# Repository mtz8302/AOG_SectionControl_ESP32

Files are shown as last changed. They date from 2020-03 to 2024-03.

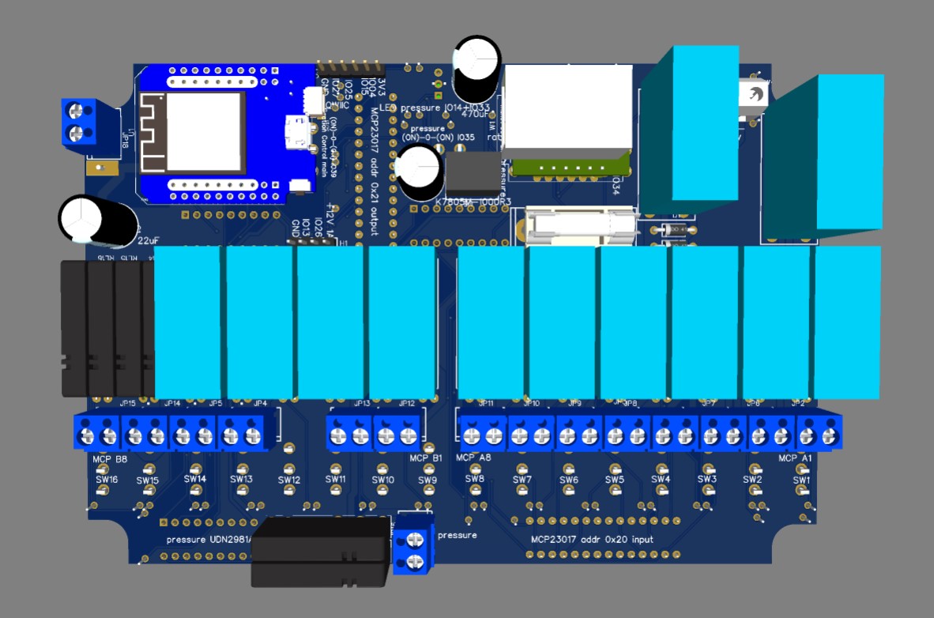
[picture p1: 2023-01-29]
Section control board 16IO/SC16IO board downside.jpg

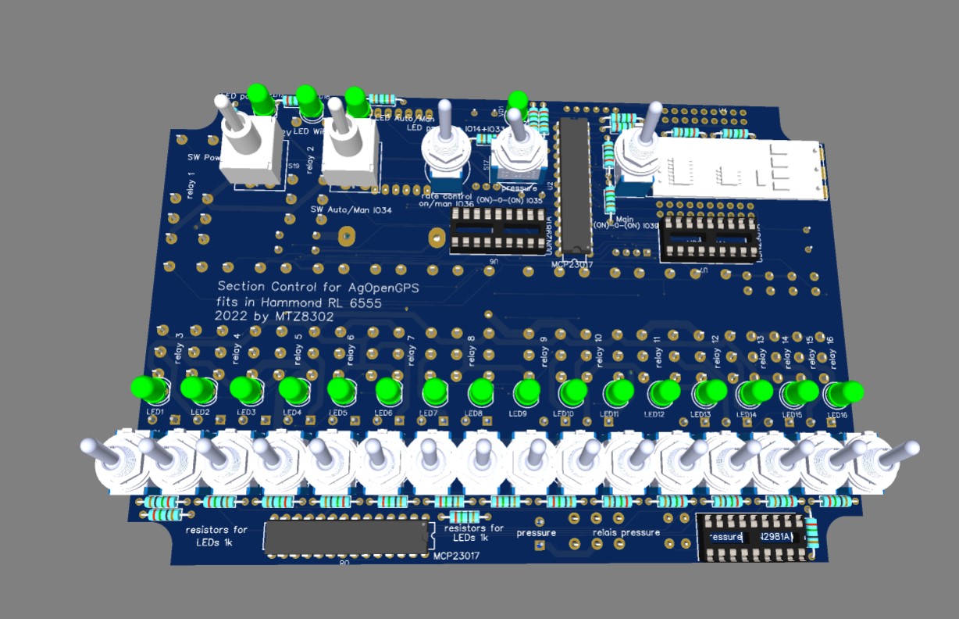
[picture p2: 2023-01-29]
Section control board 16IO/SC16IO board upside.jpg

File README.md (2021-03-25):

# AOG_Section_control

<b>Section Control running on ESP32 for AgOpenGPS PC Software.<br><br>
Multi version code: supports V 4.3.10 (=version code 17) and V5.x.20 (=version code 20)<br>
          
For existing Nano boards, the Upgrade to Nano33iot, to get WiFi is a good solution. Use code for Nano33IoT in other repository.
          
Supports: <br>- Section control, 16 sections
          <br>- hardware input switches (Main ON/OFF, OFF/Auto/ON for each section, +/- pressure (only motor driven, no rate control in V4 so far))
          <br>- documentation only (e.g. for machinery with hydraulic gates)
   <br>and most combinations of it</b>

Settings can be changed via webinterface. The IP adress is x.x.x.71 in your WiFi network. If the log to your networks fails, you wait until an accesspoint is created. Connenct your computer to it and use your browser to get to webinterface at 192.168.1.1

The settings done directly in the code are the default values, that can be reloaded. The pin assigment must be done in the code, most other things can be changed in webinterface.

Make sure, that the SSID and password fits to your tractor's WIFI.

Works with the circuit (by WEder) based on Arduino nano, see PDF.

<b>!!!The ESP32 and the Nano33 iot use 3.3V for any in-/outputs !!!</b>

A suggestion for ESP32 pinout is in the PDF. Don't use pins GPIO 0, 6-12. The pins 33-39 are input only, and don't have pullup resistors.

<b>Further remarks on the ESP32 pinout:</b><br>
The circuit could be mostly the same as in WEder's schematic.

All switches use internal pullup, so switch to GND.

GPIO 39 has no internal pullup, so external resistor 10k to 3.3V and switch to GND.

Pressure(Flowrate) and Main Switch are (ON)-OFF-(ON) switches or push buttons: 3.3V - 1.15V - GND to get 1.15V use 10k to 3.3 and 10k to GND. So only 1 input for 2 functions is needed.

For the outputs use a driver like UDN2981(relais have common GND and UDN does +) or ULN2803 (relais have common + and ULN does GND) 

Remark on non booting ESP32: they don't like raising input voltage when powering your step down 3,3V power source. To keep them in reset, put a 10uF electrolytic capacitor to reset - GND and another one EN - GND. So the enable and the reset pin will be LOW until power is stable. With this they will boot.

NO rate control in this code at the moment (not supported by AOG)

Suggestion for documentation only: https://agopengps.discourse.group/t/section-control-documentation-for-ferilizer-spreader/1360

Suggestion for upgrading Mueller spray controller: https://agopengps.discourse.group/t/muller-spray-controll-with-motor-valves/1303

Video how to use switches: https://youtu.be/kI321iBwe4U

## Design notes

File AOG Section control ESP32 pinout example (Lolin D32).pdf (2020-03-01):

## no analog Input while WiFi use (A2 occupied)

# AgOpenGPS

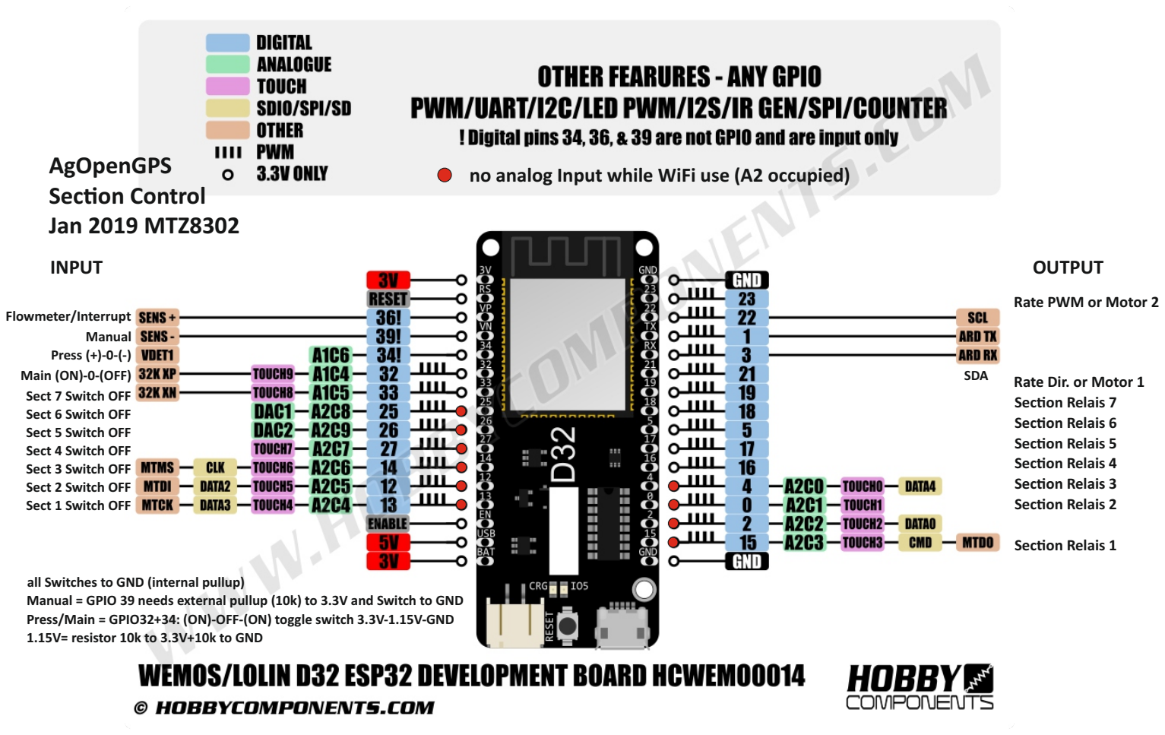
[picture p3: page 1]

SDA

## INPUT

Flowmeter/Interrupt
Manual
Press (+)-0-(-)
Main (ON)-0-(OFF)
Sect 7 Switch OFF
Sect 6 Switch OFF
Sect 5 Switch OFF
Sect 4 Switch OFF
Sect 3 Switch OFF
Sect 2 Switch OFF
Sect 1 Switch OFF

Rate Dir. or Motor 1

Rate PWM or Motor 2

Secon Relais 2

Secon Relais 1

Secon Relais 3

Secon Relais 4

Secon Relais 5

Secon Relais 6

Secon Relais 7

## OUTPUT

# Secon Control Jan 2019 MTZ8302

all Switches to GND (internal pullup)
Manual = GPIO 39 needs external pullup (10k) to 3.3V and Switch to GND Press/Main = GPIO32+34: (ON)-OFF-(ON) toggle switch 3.3V-1.15V-GND 1.15V= resistor 10k to 3.3V+10k to GND

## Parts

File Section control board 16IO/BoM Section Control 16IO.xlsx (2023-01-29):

BoM Section Control 16IO
MTZ8302
 |  |  |  |  |  |  |  |  | 2022-07-24
ID | Name | Designator | Footprint |  | Quantity | Supplier | Supplier Part | Price per unit | price | sub-total
PCB by JLCPCB |  |  |  |  | 1 | MTZ8302/JLCPCB |  | 45.00 € | 45.00 € | 45.00 €
parts for PCB
PCB - Power supply
 | 22uF | C1 | CAP-D10.0-F5.0 |  | 1 | Conrad | 468240 - 62 | 0.26 € | 0.26 €
 | 470uF | C2 | CAP-D10.0-F5.0 |  | 1 | Conrad | 468134 - 62 | 1.59 € | 1.59 €
 | 22uF | C3 | CAP-D10.0-F5.0 |  | 1 | Conrad | 468240 - 62 | 0.26 € | 0.26 €
 | 1A | F1 | FUSE-HOLDER-WITH-COVER-FOR-5X20MM-FUSE_FOOTPRINT |  | 1 | Conrad | 530127 - 62 | 0.39 € | 0.39 €
 | 1N4007GU | D2,D1 | DO-41_BD2.4-L4.7-P8.70-D0.9-RD |  | 2 | Conrad | 162272 | 0.08 € | 0.16 €
 | K7805M-1000R3 | U5 | PWRM-TH_K7805M-1000R3 |  | 1 | Digikey | 2725-7805m-1000r3-nd | 3.12 € | 3.12 €
 | 2 pol 5mm screw terminal | JP1,JP2,JP3,JP4,JP5,JP6,JP7,JP8,JP9,JP10,JP11,JP12,JP13,JP14,JP15,JP16,JP18 | SCREWTERMINAL-5MM-2 | Power + rate + 1 per section | 1 | Conrad | 1430098 | 0.40 € | 0.40 €
 | 1A fuse 5x20mm |  |  |  | 1 | Conrad | 1576534 | 0.16 € | 0.16 €
 | APEM 5546A 2x I/I | S19,S20 | SWITCH_DPDT_LEVER | Power + SC auto/man | 2 | Conrad | 700378 | 5.99 € | 11.98 €
 |  |  |  |  |  |  |  |  |  | 18.32 €
ESP32, MCP, driver, Ethernet
 | WEMOS-D1 MINI ESP32 | U1 | WEMOS-ESP32 D1 MINI |  | 1 | Amazon | WEMOS_S2_MINI | 9.98 € | 9.98 €
 | Wiznet W5500 Lite Module | W1 | W5500 LITE MODULE MINI |  | 1 | Amazon |  | 12.87 € | 12.87 €
 | UDN2981A-T | U10,U6,U7 | DIP-18_L22.9-W10.2-P2.54-LS7.6-BL |  | 3 | reichelt | UDN291 | 1.04 € | 3.12 €
 | Socket DIP-18 |  |  |  | 3 | Conrad | 189537 | 0.24 € | 0.72 €
 | MCP23017 Addr 0x20 | U8 | DIL28-3-ROUND |  | 2 | Conrad | 651440 | 1.58 € | 3.16 €
 | Socket 28pol 7,62mm | U2 |  |  | 2 | Conrad | 189515 | 0.36 € | 0.72 €
 | RS485_to_TTL_2 | U4 | RS485_TO_TTL |  | 0 | Arceli |  |  | 0.00 €
 | LED5MM | LED17,LED16,LED12,LED11,LED10,LED9,LED8,LED7,LED6,LED5,LED4,LED3,LED2,LED1,LED13,LED15,LED14 | LED5MM | 1 per section + 1 power + 1 wifi | 2 | Conrad (gn) | 1526857 | 0.28 € | 0.56 €
 |  |  |  |  |  |  |  |  |  | 31.13 €
connectors
 | 2 pol 5mm screw terminal | JP1,JP2,JP3,JP4,JP5,JP6,JP7,JP8,JP9,JP10,JP11,JP12,JP13,JP14,JP15,JP16,JP18 | SCREWTERMINAL-5MM-2 | Power + rate + 1 per section | 17 | Conrad | 1430098 | 0.40 € | 6.80 €
 | 6-PPIN-HEADER | U3 | 6-PIN-CONNECTOR-HEADER |  | 1 |  |  | 0.20 € | 0.20 €
 | SM04B-SRSS-TB(LF)(SN) | J1 | CONN-SMD_SM04B-SRSS-TB | Qwiic | 0 |  |  |  | 0.00 €
 | Header-Male-2.54_1x4 | H1 | HDR-TH_4P-P2.54-V-M |  | 1 |  |  | 0.10 € | 0.10 €
 |  |  |  |  |  |  |  |  |  | 7.10 €
parts for sections |  | 6 | sections
 | Finder-34.51.7.012.0010 | RL16,RL15,RL14,RL13,RL17,RL18 | FP_FINDER-SINGLEROW | 2x rate + section 13,14,15,16 | 0 | Conrad | 502867 | 6.49 € | 0.00 €
 | FINDER-41.52.9.012.0010 | RL12,RL11,RL10,RL9,RL8,RL7,RL6,RL5,RL4,RL3,RL2,RL1 | RELAY-FINDER-41.52 COPY | sections 1 - 12 | 6 | Conrad | 403105 | 5.54 € | 33.24 €
 | 1k | R29,R19,R18,R17,R16,R12,R11,R10,R9,R8,R7,R6,R5,R4,R3,R2,R1,R15,R14,R13,R28,R27,R26,R25,R24 | RES-TH_BD2.4-L6.3-P10.30-D0.6 |  | 10 | Conrad | 1557045 | 0.10 € | 1.00 €
 | 1k8 | R30 | RES-TH_BD2.4-L6.3-P10.30-D0.6 |  | 0 | Conrad | 1557364 | 0.10 € | 0.00 €
 | APEM 5537A 1x (I)/0/(I) | S17,S18 | SWITCH_SPDT_LEVER | SC Main on/off + rate | 2 | Conrad | 700351 | 4.29 € | 8.58 €
 | APEM 5536A 1x I/I | S21,S16,S15,S14,S13,S12,S11,S10,S9,S8,S7,S6,S5,S4,S3,S2,S1 | SWITCH_SPDT_LEVER | 1 per section + 1 rate auto/man | 6 | Conrad | 700337 | 4.29 € | 25.74 €
 | 2 pol 5mm screw terminal | JP1,JP2,JP3,JP4,JP5,JP6,JP7,JP8,JP9,JP10,JP11,JP12,JP13,JP14,JP15,JP16,JP18 | SCREWTERMINAL-5MM-2 | Power + rate + 1 per section | 6 | Conrad | 1430098 | 0.40 € | 2.40 €
 | BiColorLED-AKA | VD2,VD0 | LED_BICOL_AKA_4 |  | 1 | Conrad (ge/gn) | 1577518 | 0.59 € | 0.59 €
 | LED5MM | LED17,LED16,LED12,LED11,LED10,LED9,LED8,LED7,LED6,LED5,LED4,LED3,LED2,LED1,LED13,LED15,LED14 | LED5MM | 1 per section + 1 power + 1 wifi | 6 | Conrad (gn) | 1526857 | 0.28 € | 1.68 €
 | 10k | R23,R22,R21,R20 | RES-TH_BD2.4-L6.3-P10.30-D0.6 |  | 4 | Conrad | 400378 | 0.11 € | 0.44 €
 | LED5MM | LED17,LED16,LED12,LED11,LED10,LED9,LED8,LED7,LED6,LED5,LED4,LED3,LED2,LED1,LED13,LED15,LED15 | LED5MM |  | 0 | Conrad (ge) | 1603104 | 0.15 € | 0.00 €
 |  |  |  |  |  |  |  |  |  | 73.67 €
parts for rate
 | Finder-34.51.7.012.0010 | RL16,RL15,RL14,RL13,RL17,RL18 | FP_FINDER-SINGLEROW | 2x rate + section 13,14,15,16 | 2 | Conrad | 502867 | 6.49 € | 12.98 €
 | APEM 5537A 1x (I)/0/(I) | S17,S18 | SWITCH_SPDT_LEVER | rate +/- | 1 | Conrad | 700351 | 4.29 € | 4.29 €
 | APEM 5536A 1x I/I | S21,S16,S15,S14,S13,S12,S11,S10,S9,S8,S7,S6,S5,S4,S3,S2,S1 | SWITCH_SPDT_LEVER | rate auto/man | 1 | Conrad | 700337 | 4.29 € | 4.29 €
 | 2 pol 5mm screw terminal | JP1,JP2,JP3,JP4,JP5,JP6,JP7,JP8,JP9,JP10,JP11,JP12,JP13,JP14,JP15,JP16,JP18 | SCREWTERMINAL-5MM-2 | Power + rate + 1 per section | 1 | Conrad | 1430098 | 0.40 € | 0.40 €
 | BiColorLED-AKA | VD2,VD1 | LED_BICOL_AKA_5 |  | 1 | Conrad (rt/gn) | 1577346 | 0.59 € | 0.59 €
 |  |  |  |  |  |  |  |  |  | 22.55 €
housing
 | hammond 6555 |  |  |  | 1 | conrad | 531864 | 10.55 € | 10.55 €
 |  |  |  |  |  |  |  |  |  | 10.55 €
 |  |  |  |  |  |  |  |  |  |  | 208.32 € | PCB with components and box
cabeling
 | 2 x 2.5 Lapp Ölflex classic 110 |  |  | power supply | 2 | conrad | 601836 | 3.29 € | 6.58 €
 | 25G 0.75 Ölflex classic 110 |  | maybe less wires | box to sprayer | 6 | conrad | 600248 | 9.49 € | 56.94 €
 | M16 Lapp Kabelverschraubung |  |  |  | 1 | Conrad | 127713 | 1.29 € | 1.29 €
 | M25 Lapp Kabelverschraubung |  |  |  | 2 | Conrad | 527739 | 2.29 € | 4.58 €
 |  |  |  |  |  |  |  |  |  | 69.39 €
connector for Arag
 | Hirschmann GM 209 NJ |  |  |  | 8 | Conrad | 734958 | 2.79 € | 22.32 €
 |  |  |  |  |  |  |  |  |  | 22.32 €
power connector
 | Hella 8JA 002 263-011 |  |  |  | 1 |  |  | 9.63 € | 9.63 €
 |  |  |  |  |  |  |  |  |  | 9.63 €
 |  |  |  |  |  |  |  |  |  | 309.66 €

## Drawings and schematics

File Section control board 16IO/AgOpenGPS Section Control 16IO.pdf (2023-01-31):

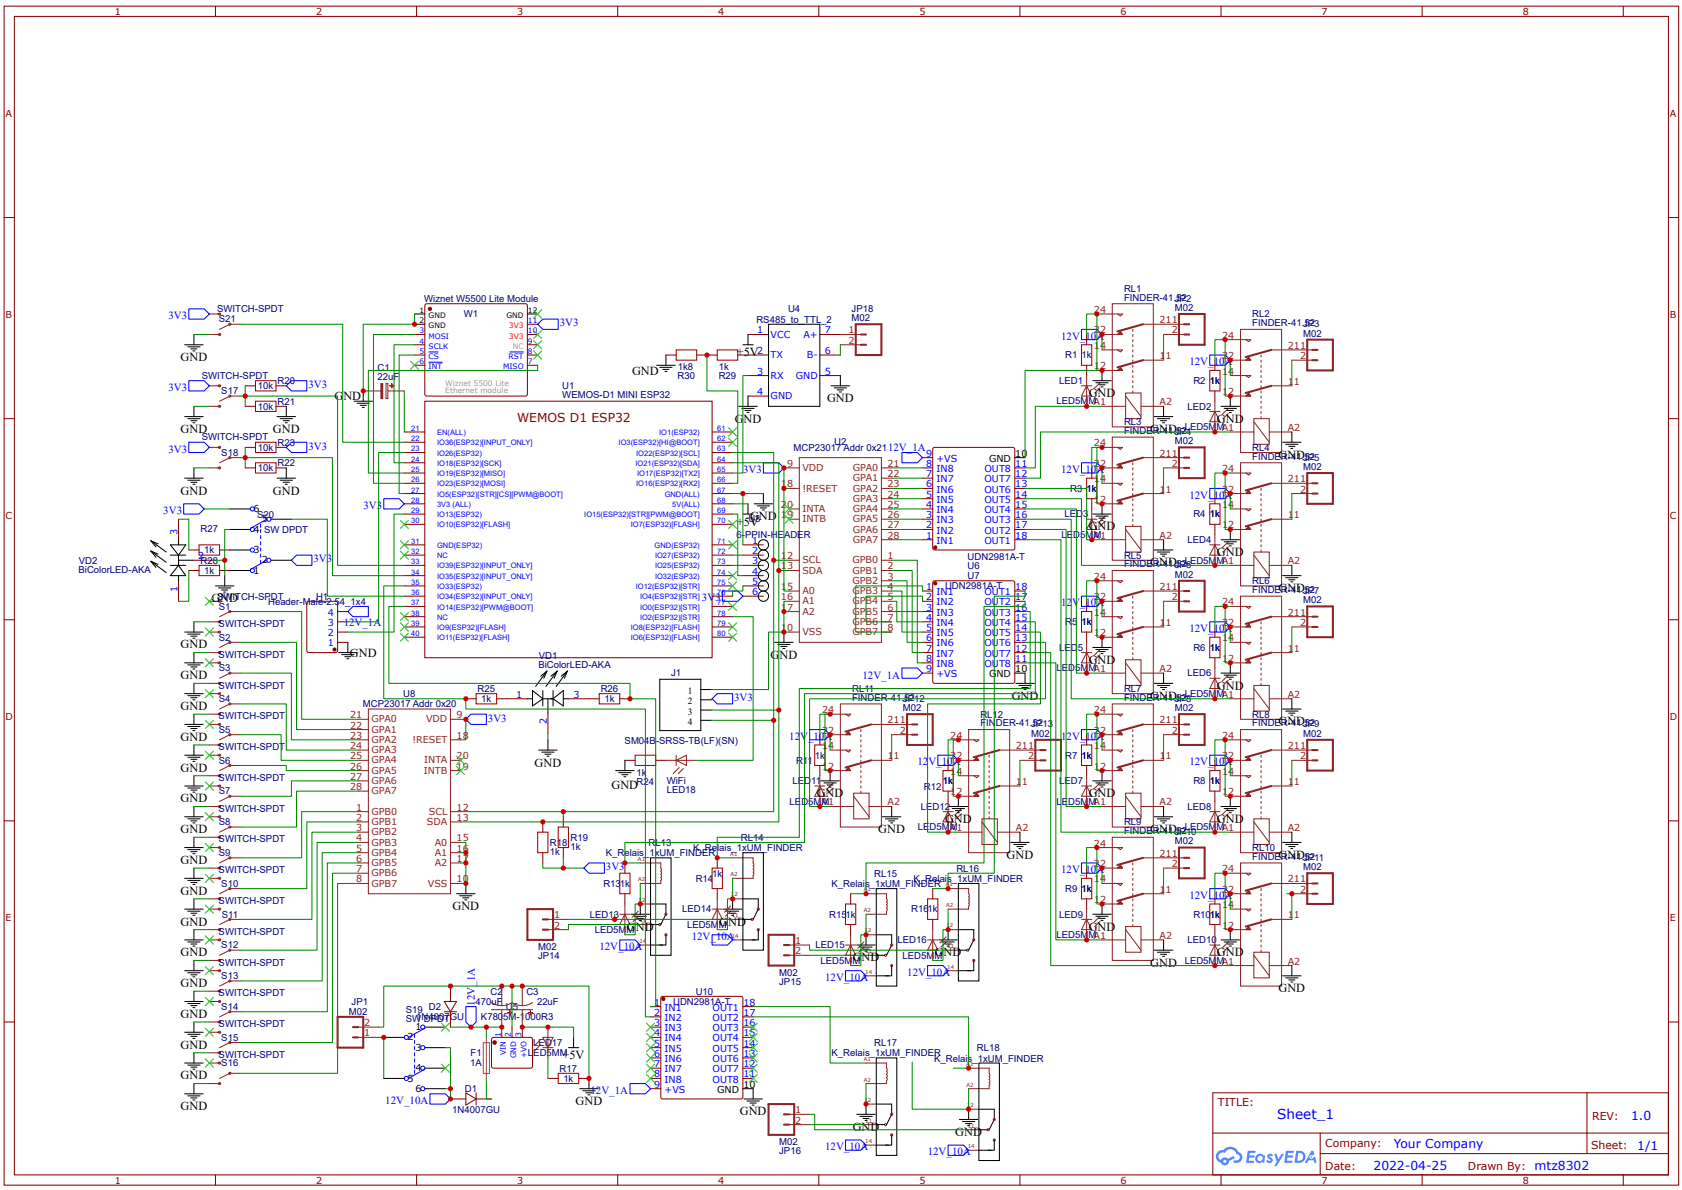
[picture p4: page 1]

SM04B-SRSS-TB(LF)(SN)

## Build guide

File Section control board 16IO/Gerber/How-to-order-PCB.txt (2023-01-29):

How to Order PCB

Please refer to:
https://docs.easyeda.com/en/PCB/Order-PCB

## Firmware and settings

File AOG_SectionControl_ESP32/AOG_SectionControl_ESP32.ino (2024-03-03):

// Section Control code for AgOpenGPS V5 or later for ESP32

// by MTZ8302 see GitHub https://github.com/mtz8302 and Youtube Ma Ha MTZ8302 https://www.youtube.com/channel/UCv44DlUXQJKbQjzaOUssVgw

// can be used as output only = relais for sections
// or for documentation = input only = input to ESP32 -> enables mapping for active (=switch to GND) section in AOG
// or any combination = section control with input switch
// main and pressure switches are (ON)-0-(ON) toggle switches (GND)- 1.75V - (3,3V). So use 2 resistors GND- 1K - (COM on toggle switch) - 1K - 3.3V
// section switches and auto/manual switch are ON-OFF switches

// connects to existing WiFi network or creates access point. Settings below or in WebInterface at 192.168.1.71 in access point mode Webinterface at 192.168.1.1

// while startup ESP32 sends debug infos to USB at 38400 baud

byte vers_nr = 58;
char VersionTXT[150] = " - 28. Feb 2024 by MTZ8302<br>PCA9555, AgIO Heartbeat, AsyncUDP for WiFi, multiple WiFi networks, Ethernet support";


struct set {
	//User config: ***********************************************************************************

	uint8_t DataTransVia = 10;		//transfer data via 0 = USB / 7 = WiFi / 10 = Ethernet UDP
	uint8_t aogVersion = 20;		// not used at the moment
	uint8_t AgIOHeartbeat_answer = 1;//0: don't send (default)
	uint8_t LEDWiFi_PIN = 2;		// WiFi Status LED 255 = off
	uint8_t LEDWiFi_ON_Level = 1;   // 1 = HIGH = LED on high, 0 = LOW = LED on low

	//WiFi---------------------------------------------------------------------------------------------
	//tractors WiFi or mobile hotspots. Connections are checked in this order
	char ssid1[24] = "Matthias A53";	// WiFi network Client name
	char password1[24] = "aveasillrac";                // WiFi network password//Accesspoint name and password
	char ssid2[24] = "Deutz_6006";			// WiFi network Client name
	char password2[24] = "";                // WiFi network password//Accesspoint name and password
	char ssid3[24] = "Fendt_209V_Tablet";					// WiFi network Client name
	char password3[24] = "Fendt_209V";                // WiFi network password//Accesspoint name and password
	char ssid4[24] = "Fendt_209V";					// WiFi network Client name
	char password4[24] = "";                // WiFi network password//Accesspoint name and password
	char ssid5[24] = "WLANHammer";					// WiFi network Client name
	char password5[24] = "aveasillrac";                // WiFi network password//Accesspoint name and password

	char ssid_ap[24] = "SectionControlNet"; // name of Access point, if no WiFi found, no password!!
	uint8_t timeoutRouter = 20;//s         // time (s) to search for existing WiFi, then starting Accesspoint 
	byte timeoutWebIO = 10;//min  		    // time (min) afterwards webinterface is switched off	
	uint8_t timeoutRouterEth = 255;//s		// time (s) to search for Ethernet cable, then changing datatransfer to WiFi

	//WiFi
	byte WiFi_myip[4] = { 192, 168, 137, 71 };    // Section Control 
	byte WiFi_gwip[4] = { 192, 168, 1, 1 };     // Gateway IP only used if Accesspoint created
	byte WiFi_ipDest_ending = 255;				//ending of IP address to send UDP data to
	byte mask[4] = { 255, 255, 255, 0 };
	byte myDNS[4] = { 8, 8, 8, 8 };				//optional

	//Ethernet
	byte Eth_myip[4] = { 192, 168, 5, 72 };     // Section Control 
	byte Eth_ipDest_ending = 255;				// ending of IP address to send UDP data to
	byte Eth_mac[6] = { 0x90,0xA2,0xDA,0x10,0xB3,0x1B };
	bool Eth_static_IP = false;					// false = use DHPC and set last number to 80 (x.x.x.80) / true = use IP as set above

	uint16_t PortSCToAOG = 5555;			// this is port of this module: Autosteer = 5577 IMU = 5566 Section Control = 5555 GPS = 5544
	uint16_t PortFromAOG = 8888;            // port to listen for AOG
	uint16_t PortDestination = 9999;        // Port of AOG that listens
	uint16_t BaudRate = 38400;              // Baudrate = speed of serial port or USB or Bluetooth. AOG uses 38400 for UART

//the following lines should be configed by the user to fit the programm to the sprayer/ESP32
//GPIOs of the ESP32 (current setting is for the layout shown as example WIKI)

	byte Eth_CS_PIN = 5;// 13;					// CS PIN with SPI Ethernet hardware  SPI config: MOSI 23 / MISO 19 / CLK18 / CS5
	byte Eth_INT_PIN = 255;                 //interupt pin not used at the moment, but needed if async ethernet lib will be used

// if only 1 flowrate is used, use left
//Example1: motor valve is controled only by Switch not by AOG, no Flowmeter, : RateControl..Equiped = false; RateSW..Equiped = true; RateControlPWM = false;
//Example2: PWM valve, with flowmeter all controled by AOG:   RateControl..Equiped = true; RateSW..Equiped = true; RateControlPWM = true;	
	uint8_t RateControlLeftInst = 0;		// 1 if Rate control is there, else: 0
	uint8_t RateSWLeftInst = 1;				// 1 if Rate control Pressure switch is there, else: 0
	uint8_t RateSWLeft_PIN = 39;// 34;			// Rate +/- switch (ON)-0-(ON) toggle switch (GND)- 1.75V - (3,3V)
	uint8_t RateControlPWM = 0;				// 1 if PWM valve, 0 if Motor drive for pressure change		

	uint8_t	FlowDirLeft_PIN = 32;// 23;			// Rate-Control Valve/Motor Direktion
	uint8_t	FlowPWMLeft_PIN = 33;// 22;			// Rate-Control Valve PWM/Motor ON/OFF
	uint8_t	FlowEncALeft_PIN = 255;			// Flowmeter left/1

	uint8_t RateControlRightInst = 0;	    // 1 if Rate control is there, else: 0
	uint8_t RateSWRightInst = 0;			// 1 if Rate control Pressure switch is there, else: 0	
	uint8_t	RateSWRight_PIN = 255;			// Rate +/- switch
	uint8_t	FlowDirRight_PIN = 255;			// 255  = unused Rate-Control Valve Direktion
	uint8_t	FlowPWMRight_PIN = 255;			// 255  = unused Rate-Control Valve PWM
	uint8_t	FlowEncARight_PIN = 255;		// Flowmeter right/2 

	uint8_t SectNum = 16;					// number of sections
	uint8_t SectRelaysInst = 1;				// relays for SC output are equiped (0=no output, only documentation)
	uint8_t SectRelaysON = 1;				// relays spray on 1 or 0 (high or low)
	//Relay_PIN = GPIOs of ESP32 OUT to sections of sprayer, 255 = unused, 100 = pin IO 1 on PCA9555 116 = pin IO 16 on PCA9555
	uint8_t Relay_PIN[16] = { 100,101,102,103,104,105,106,107,108,109,110,111,112,113,114,115 };// { 15, 2, 0, 4, 16, 17, 18, 19, 21, 255, 255, 255, 255, 255, 255, 255 };
	uint8_t Relais_MainValve_PIN = 0;// 255;		// PIN for Main fluid valve 255 = unused
	
	uint8_t SectSWInst = 1;					// 1 if section input switches are equiped, else: 0	
	uint8_t SectSWAutoOrOn = 1;				// Section switches spray/auto on 1 = high = used with pullup, 0 = low = pulldown 
	uint8_t SectSW255Stat = 2;				// not present switches (255) send 0 = auto, 1 = on, 2 = off, (comming soon: 3 = undefined) 
	//section switches to GPIOs of ESP32, 255 = unused, 100 = pin IO 1 on PCA9555 116 = pin IO 16 on PCA9555
	uint8_t SectSW_PIN[16] = { 100,101,102,103,255,105,106,107,108,255,110,111,112,113,114,115 };// { 255, 12, 14, 27, 26, 25, 33, 255, 36, 255, 255, 255, 255, 255, 255, 255 };
	uint8_t	SectMainSWType = 1;				// 0 = not equiped 1 = (ON)-OFF-(ON) toggle switch or push buttons 2 = connected to hitch level sensor 3 = inverted hitch level sensor
	uint16_t	HitchLevelVal = 2000;		// Value for hitch level: switch AOG section control to Auto if lower than... ESP:2000 nano 500
	uint8_t	SectMainSW_PIN = 35;// 32;			// ESP32 to AOG Main auto toggle switch open=+1,9V=nothing/AOG button GND=OFF +3,3=AOG Auto on	OR connected to hitch level sensor	
	uint8_t	SectAutoManSW_PIN = 34;// 39;			// Main Auto/Manual switch 39:!!no internal pullup!!

	uint8_t DualFluidSW_PIN = 255;			//not supported at the moment
	uint8_t OnOffDelayAutoManSW_PIN = 255;	//not supported at the moment
	uint8_t OnDelayDist_dm = 30;			//not supported at the moment
	uint8_t OffDelayDist_dm = 35;			//not supported at the moment

	uint8_t DocOnly = 0;					// 0: use as section control, 1: Documentation only = AOG writes the state of the input switches

	uint8_t I2CAddrPCAInput = 0x20;
	uint8_t I2CAddrPCAOutput = 0x21;

	uint8_t resByte0 = 0;
	uint8_t resByte1 = 0;
	uint8_t resByte2 = 0;
	uint8_t resByte3 = 0;

	uint16_t resInt0 = 0;
	uint16_t resInt1 = 0;

	bool debugmode = false;
	bool debugmodeRelay = false;
	bool debugmodeSwitches = false;
	bool debugmodeDataFromAOG = false;
	bool debugmodeDataToAOG = false;

	// END of user config ****************************************************************************
}; set Set;


bool EEPROM_clear = false;



byte SCToAOG[14] = { 0,0,0,0,0,0,0,0,0,0,0,0,0,0 }, SCToAOGOld[14] = { 0,0,0,0,0,0,0,0,0,0,0,0,0,0 };
uint8_t helloFromSC[] = { 128, 129, 123, 123, 5, 0, 0, 0, 0, 0, 71 }; //hello from SC sent back to AgIO

const byte FromAOGSentenceHeader[3] = { 0x80,0x81,0x7F };
#define FromSCHeader 0x7B
#define SCDataToAOGHeader  0xEA
#define SteerDataFromAOGHeader  0xFE  //take section info from steer packet
#define SCSettingsFromRCHeader  0xFC
#define AgIO_heartbeat 0xC8
#define AgIO_ScanRequest 0xCA//AgIO asking for IP -> Ethernet/WiFi GPS sends IP 
#define SCDataSentenceToAOGLength  14

//write incoming Data to sentence array if it fits in
#define SentenceFromAOGMaxLength 14
byte SentenceFromAOG[SentenceFromAOGMaxLength], SentenceFromAOGLength;

//global, as serial/USB may not come at once, so values must stay for next loop
byte incomSentenceDigit = 0,DataToAOGLength;
bool isSteerDataFound = false, isRCSettingFound = false, isAgIOHeartbeatFound = false, isAgIOScanRequestFound = false;

#define incommingDataArraySize 10
byte incommingBytes[incommingDataArraySize][500], incommingBytesArrayNr = 0, incommingBytesArrayNrToParse = 0;
unsigned int incommingDataLength[incommingDataArraySize] = { 0,0,0,0,0 };

//WIFI+Ethernet
IPAddress WiFi_ipDestination, Eth_ipDestination; //set in network.ino
byte Eth_connect_step, WiFi_connect_step = 10, WiFi_netw_nr = 0, WiFi_STA_connect_call_nr = 0, my_WiFi_Mode = 0; // WIFI_STA = 1 = Workstation  WIFI_AP = 2  = Accesspoint
//int pingResult, WiFiWatchDog = 0;
bool WiFiUDPRunning = false, EthUDPRunning = false, task_WiFiConnectRunning = false;
unsigned long WebIOTimeOut = 0, WiFi_network_search_timeout = 0, Eth_network_search_timeout = 0;//PingToNetworkLastTime = 0,
//webpage
long argVal = 0;
bool WebIORunning = false;

// WiFi LED blink times: searching WIFI: blinking 4x faster; connected: blinking as times set; data available: light on; no data for 2 seconds: blinking
unsigned int LED_WIFI_time = 0;
unsigned int LED_WIFI_pulse = 2000;   //light on in ms 
unsigned int LED_WIFI_pause = 1500;   //light off in ms
boolean LED_WIFI_ON = false;
unsigned long timeout, timeout2;



//ToDo: - Rate / flowmeter doesn't work, interrupt mode ect not defined
//      - line 260 PWM + Interrupt mode ect...
//		  - Right side Rate caluclation / output / Motordrive
//      - Manual mode for Rate Control
//		  - what to do if no WIFI??


//libraries -------------------------------
#include "EEPROM.h"
#include "Update.h"
#include <WiFi.h>
#include <AsyncUDP.h>
#include <WebServer.h>
#include <Wire.h>
#include <Ethernet.h>
#include "zAOG_ESP32Ping.h"
#include "zAOG_ping.h"

WebServer WiFi_Server(80);
AsyncUDP WiFiUDPFromAOG;
AsyncUDP WiFiUDPToAOG;
EthernetUDP EthUDPToAOG;
EthernetUDP EthUDPFromAOG;
TaskHandle_t taskHandle_Eth_connect;
TaskHandle_t taskHandle_WiFi_connect;
TaskHandle_t taskHandle_DataFromAOGUSB; bool USBDataTaskRunning = false;
TaskHandle_t taskHandle_DataFromAOGEth; bool EthDataTaskRunning = false;
TaskHandle_t taskHandle_WebIO;
TaskHandle_t taskHandle_LEDBlink;


//values to decide position of section switch
#define SWOFF 650 // analog in is lower than .. for off
#define SWON 3000 // analog in is lower than .. for auto/on


//analog value of the toggle switches (default: middle=unpressed)
int MainSWVal = (SWOFF + SWON) / 2;
int MainSWValOld = (SWOFF + SWON) / 2;
int RateSWLeftVal = (SWOFF + SWON) / 2;
int RateSWRightVal = (SWOFF + SWON) / 2;

//state of the switches HIGH = ON/Auto LOW = OFF	
boolean SectSWVal[16] = { HIGH,HIGH,HIGH,HIGH,HIGH,HIGH,HIGH,HIGH,HIGH,HIGH,HIGH,HIGH,HIGH,HIGH,HIGH,HIGH };
boolean AutoSWVal = HIGH;
byte debugmodeSwitchesBak = 3;  //0 = false 1 = true 3 = not used

//loop time variables in microseconds
const unsigned long LOOP_TIME = 500; //in msec; 1000 = 1 Hz
const unsigned long SectSWDelayTime = 200;//time the arduino waits after manual Switch is used before acception command from AOG in msec
unsigned long lastTime = LOOP_TIME;
unsigned long now = LOOP_TIME;
unsigned long DataFromAOGTime = 0;
unsigned long SectAutoSWTime = LOOP_TIME;
unsigned long SectAutoSWlastTime = LOOP_TIME;
unsigned long SectMainSWlastTime = LOOP_TIME;
unsigned long RateSWlastTimeLeft = LOOP_TIME;
unsigned long RateSWDelayTime = 250; //time to pass before a new toggle of switch is accepted = if hold down, time between steps
unsigned long RateSWlastTimeRight = LOOP_TIME;
unsigned long SectSWcurrentTime = LOOP_TIME;


/* no rate control in AOG
//Kalman variables Left
float rateKLeft = 0;
float PcLeft = 0.0;
float GLeft = 0.0;
float PLeft = 1.0;
float XpLeft = 0.0;
float ZpLeft = 0.0;
float XeRateLeft = 0; //the filtered flowrate
const float varRateLeft = 100; // variance, smaller, more filtering
const float varProcessLeft = 10;

//Kalman variables Right
float rateKRight = 0;
float PcRight = 0.0;
float GRight = 0.0;
float PRight = 1.0;
float XpRight = 0.0;
float ZpRight = 0.0;
float XeRateRight = 0; //the filtered flowrate
const float varRateRight = 100; // variance, smaller, more filtering
const float varProcessRight = 10;
*/

//program flow
//bool NewDataFromAOG = false, NewSettingFromAOG = false;

//bit 0 on byte[0] is section 1
byte SectGrFromAOG[] = { 0, 0 }; //Sections ON / OFF Bitwise !!! 
byte RelayOUT[] = { 0,0 }; //Sections ON / OFF Bitwise !!! 
byte RelayOUTOld[] = { 0,0 };
byte SectSWOffToAOG[] = { 0,0 };
byte SectMainToAOG = 0;
byte uTurnRelay = 0;
//  byte flowRateSW1 = 0;
boolean PCAinUse = false;
boolean SectMainSWpressed = false;
boolean SectSWpressed = false;
boolean SectSWpressedLoop = false;
boolean SectAuto = true;
boolean SectAutoOld = true;
boolean SectAutoSWpressed = false;
//boolean RateAuto = false;
boolean RateManUpLeft = false;
boolean RateManUpRight = false;
boolean RateManDownLeft = false;
boolean RateManDownRight = false;

boolean SectMainOn = false;

boolean newDataToAOG = false;// newDataFromAOG = false;

float gpsSpeed = 0; //speed from AgOpenGPS
float rateSetPointLeft = 0.0;
float countsThisLoopLeft = 0;
float rateErrorLeft = 0; //for PID
int rateAppliedLPMLeft = 0;
float rateSetPointRight = 0.0;
float countsThisLoopRight = 0;
float rateErrorRight = 0; //for PID
int rateAppliedLPMRight = 0;

unsigned long accumulatedCountsLeft = 0;
float flowmeterCalFactorLeft = 50;
unsigned long accumulatedCountsRight = 0;
float flowmeterCalFactorRight = 50;
unsigned long accumulatedCountsDual = 0;

float pulseAverageLeft = 0;
float pulseAverageRight = 0;

//the ISR counter
volatile unsigned long pulseCountLeft = 0, pulseDurationLeft;
volatile unsigned long pulseCountRight = 0, pulseDurationRight;
bool state = false;



void setup()
{	delay(100);//wait for power to stabilize
	delay(100);//wait for IO chips to get ready
	//set up communication
	Serial.begin(Set.BaudRate);
	delay(10);
	delay(50);
	Serial.println();
	//get EEPROM data
	restoreEEprom();
	delay(100);

	SCToAOG[0] = FromAOGSentenceHeader[0];   //0x80
	SCToAOG[1] = FromAOGSentenceHeader[1];   //0x81
	SCToAOG[2] = FromSCHeader;				 //0x7B
	SCToAOG[3] = SCDataToAOGHeader;			 //0xEA
	SCToAOG[4] = SCDataSentenceToAOGLength - 6; //length of data = all - header - length - CRC
	SCToAOGOld[0] = FromAOGSentenceHeader[0];
	SCToAOGOld[1] = FromAOGSentenceHeader[1];
	SCToAOGOld[2] = FromSCHeader;
	SCToAOGOld[3] = SCDataToAOGHeader;
	SCToAOG[4] = SCDataSentenceToAOGLength - 6;
	DataToAOGLength = SCDataSentenceToAOGLength;
	incomSentenceDigit = 0;

	Serial.println();
	Serial.print("ESP code Version Nr ");
	Serial.print(vers_nr);
	Serial.println(VersionTXT);
	Serial.println();

	//set GPIOs
	assignGPIOs();
	delay(50);

	//switches -> set relais
	if ((Set.SectSWInst) || (Set.SectMainSWType != 0)) {
		SectSWRead();
	}
	SetRelays();

	//Rate switches and motor drive
	if ((Set.RateSWLeftInst == 1) || (Set.RateSWRightInst == 1)) { RateSWRead(); }
	if (Set.RateControlLeftInst == 0) { motorDrive(); } //if Manual do everytime, not only in timed loop

	//start Ethernet
	if (Set.DataTransVia == 10) {
		Eth_connect_step = 10;
		xTaskCreate(Eth_handle_connection, "EthConnectHandle", 3072, NULL, 1, &taskHandle_Eth_connect);
		delay(500);
	}
	else { Eth_connect_step = 255; }
	
	WiFi_connect_step = 10;//step 10 = begin of starting a WiFi connection
	//start WiFi
	xTaskCreate(WiFi_handle_connection, "WiFiConnectHandle", 3072, NULL, 1, &taskHandle_WiFi_connect);
	delay(500);

	//get Data via USB;   WiFi not needed as AsyncUDP, Ethernet started in Ethernet connection task
	if (Set.DataTransVia < 5) {//USB
		xTaskCreate(getDataFromAOGUSB, "DataFromAOGHandleUSB", 5000, NULL, 1, &taskHandle_DataFromAOGUSB);
	}
	delay(500);

	//handle WiFi LED status
	xTaskCreate(WiFi_LED_blink_and_Connection_check, "WiFiLEDBlink", 3072, NULL, 0, &taskHandle_LEDBlink);
	delay(500);

	vTaskDelay(500); //waiting for other tasks to start

	if (Set.DataTransVia > 5) {//waiting for other tasks to start (6 s) and read switches at 4 Hz
		for (byte i = 0; i < 24; i++) {
			//switches -> set relais
			if ((Set.SectSWInst) || (Set.SectMainSWType != 0)) { SectSWRead(); }
			SetRelays();

			//Rate switches and motor drive
			if ((Set.RateSWLeftInst == 1) || (Set.RateSWRightInst == 1)) { RateSWRead(); }
			if (Set.RateControlLeftInst == 0) { motorDrive(); } //if Manual do everytime, not only in timed loop

			vTaskDelay(250);
		}
	}

}  //end setup


//-------------------------------------------------------------------------------------------------

void loop() {

	//new data from AOG? Data comes via extra task and is written into byte array. Parsing called here
	for (;;) {
		if (incommingBytesArrayNr == incommingBytesArrayNrToParse) {
			vTaskDelay(4);//3 wait if no new data to give time to other tasks 
			break;
		}
		else { parseDataFromAOG(); }
	}

	//read switches/inputs
	if ((Set.SectSWInst) || (Set.SectMainSWType != 0))
	{
		SectSWRead(); //checks if section switch is toggled and sets RelayOUT

		//reset debugSwitches: has been change to true, if debugmodeDataToAOG = true for 1 loop
		if ((Set.debugmodeSwitches) && (debugmodeSwitchesBak == 0)) { Set.debugmodeSwitches = false; }

		SCToAOG[10] |= SectSWOffToAOG[0]; //LowByte if bit set -> AOG section forced off
		SCToAOG[12] |= SectSWOffToAOG[1]; //HiByte if bit set -> AOG section forced off
		SCToAOG[5] = SectMainToAOG; // Bits: AOG section control AUTO, Section control OFF, Rate L+R ...
		//new data?
		for (byte idx = 5; idx < DataToAOGLength; idx++) {
			if (SCToAOG[idx] != SCToAOGOld[idx]) {
				newDataToAOG = true;
				SCToAOGOld[idx] = SCToAOG[idx];
			}
		}
	}
	//no switches: set Relais as AOG commands
	else { RelayOUT[0] = SectGrFromAOG[0]; RelayOUT[1] = SectGrFromAOG[1]; }

	SetRelays();


	//Rate switches and motor drive
	if ((Set.RateSWLeftInst == 1) || (Set.RateSWRightInst == 1)) { RateSWRead(); }

	if (Set.RateControlLeftInst == 0) { motorDrive(); } //if Manual do everytime, not only in timed loop


//timed loop: runs with 1Hz or if new data from switches to send data to AOG
//must run, also if nothing changed on switches, to keep GUI syncron (important if a section switch is off)
	now = millis();
	if ((now > LOOP_TIME + lastTime) || (newDataToAOG)) {
		lastTime = now;

		//add the checksum
		int CRCtoAOG = 0;
		for (byte i = 2; i < sizeof(SCToAOG) - 1; i++)
		{
			CRCtoAOG = (CRCtoAOG + SCToAOG[i]);
		}
		SCToAOG[sizeof(SCToAOG) - 1] = CRCtoAOG;

		AOGDataSend();
		if (newDataToAOG) {
			vTaskDelay(5);
			newDataToAOG = false;
			AOGDataSend(); //send 2. time for safety
		}

		if (Set.debugmodeDataToAOG) {
			Serial.print("Data to AOG ");
			for (byte n = 0; n < DataToAOGLength; n++) {
				Serial.print(SCToAOG[n]); Serial.print(" ");
			}
			Serial.println();
			//printing swich input 1x:
			if (!Set.debugmodeSwitches) {
				debugmodeSwitchesBak = 0;
				Set.debugmodeSwitches = true;
			}
			else debugmodeSwitchesBak = 1;
		}

	}
}

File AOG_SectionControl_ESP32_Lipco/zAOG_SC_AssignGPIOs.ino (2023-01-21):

void assignGPIOs() {
	//Lipco mod	
	if (Set.FronttankSW_PIN < 255) { pinMode(Set.FronttankSW_PIN, INPUT_PULLUP); }
	else { Serial.println("no PIN set for Fronttank switch"); }
	if (Set.TunnelLeftSW_PIN < 255) { pinMode(Set.TunnelLeftSW_PIN, INPUT_PULLUP); }
	else { Serial.println("no PIN set for left Tunnel switch"); }
//	if (Set.TunnelRightNarrowerSW_PIN < 255) { pinMode(Set.TunnelRightNarrowerSW_PIN, INPUT_PULLUP); }
//	else { Serial.println("no PIN set for right tunnel narrower switch"); }
//	if (Set.TunnelRightWiderSW_PIN < 255) { pinMode(Set.TunnelRightWiderSW_PIN, INPUT_PULLUP); }
//	else { Serial.println("no PIN set for right tunnel wider switch"); }

	if (Set.MCPInUse) {
		if (!Wire.begin()) { Serial.println("error INIT wire, MCP23017 will not work"); }
		delay(500);//needed for wire to init

		//cmp23017 init
		//input
		Wire.beginTransmission(0x20);
		Wire.write(0x00); // IODIRA register
		Wire.write(0xFF); // set all of port A to inputs
		Wire.endTransmission();
		Wire.beginTransmission(0x20);
		Wire.write(0x01); // IODIRB register
		Wire.write(0xFF); // set all of port B to inputs
		Wire.endTransmission();
		Wire.beginTransmission(0x20);
		Wire.write(0x0C); // GPPUA register pullup
		Wire.write(0xFF); // set all pullups active
		Wire.endTransmission();
		Wire.beginTransmission(0x20);
		Wire.write(0x0D); // GPPUB register pullup
		Wire.write(0xFF); // set all pullups active
		Wire.endTransmission();

		//output
		Wire.beginTransmission(0x21);
		Wire.write(0x00); // IODIRA register
		Wire.write(0x00); // set all of port A to outputs
		Wire.endTransmission();
		Wire.beginTransmission(0x21);
		Wire.write(0x01); // IODIRB register
		Wire.write(0x00); // set all of port B to outputs
		Wire.endTransmission();
		Wire.beginTransmission(0x21);
		Wire.write(0x0C); // GPPUA register pullup
		Wire.write(0xFF); // set all pullups active
		Wire.endTransmission();
		Wire.beginTransmission(0x21);
		Wire.write(0x0D); // GPPUB register pullup
		Wire.write(0xFF); // set all pullups active
		Wire.endTransmission();


		/*	mcpForInput.init();
			delay(100);
			mcpForInput.portMode(MCP23017Port::A,
				0b11111111,   // direction (IODIRB) - set direction of all pins as inputs
				0b11111111,   // pull-up (GPPUB) - enable 100K pull-up resistors on all inputs
				0b00000000);  // polarity (IPOLB) - don't invert logic polarity for all inputs
			mcpForInput.portMode(MCP23017Port::B,
				0b11111111,   // direction (IODIRB) - set direction of all pins as inputs
				0b11111111,   // pull-up (GPPUB) - enable 100K pull-up resistors on all inputs
				0b00000000);  // polarity (IPOLB) - don't invert logic polarity for all inputs
			delay(20);
			mcpForOutput.init();
			delay(100);
			mcpForOutput.portMode(MCP23017Port::A,
				0b00000000);  // direction (IODIRA) - set direction of all pins as outputs
			mcpForOutput.portMode(MCP23017Port::B,
				0b00000000);  // direction (IODIRA) - set direction of all pins as outputs
			mcpForOutput.writeRegister(MCP23017Register::GPIO_A, 0x00);  //Reset port A
			mcpForOutput.writeRegister(MCP23017Register::GPIO_B, 0x00);  //Reset port B
			*/
	}

	for (int i = 0; i < Set.SectNum; i++)
	{
		if (Set.SectSWInst) {
			if (Set.SectSW_PIN[i] < 100) { pinMode(Set.SectSW_PIN[i], INPUT_PULLUP); }
			else {
				if (Set.SectSW_PIN[i] == 255) { Serial.print("no PIN set for section switch #"); Serial.println(i + 1); }
			}
		}
		if (Set.Relay_PIN[i] < 100) { pinMode(Set.Relay_PIN[i], OUTPUT); }
		else {
			if (Set.SectSW_PIN[i] == 255) { Serial.print("no PIN set for section relay #"); Serial.println(i + 1); }
		}
	}
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

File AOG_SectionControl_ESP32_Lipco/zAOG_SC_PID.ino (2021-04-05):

/*
contains rate control, not included in AOG actually

void Core1code(void * pvParameters) {
	for (;;)

		// MAIN LOOP FOR THIS CORE
	{
		//delay(0); //do WIFI stuff
		now = millis();
		unsigned int time = now;

		//timed loop
		if ((now - lastTime >= LOOP_TIME) || SectSWpressed)
		{
			dT = now - lastTime;
			lastTime = now;

			//reset ISR Left Side
			countsThisLoopLeft = pulseCountLeft;
			pulseCountLeft = 0;

			if (countsThisLoopLeft)
			{
				//total pulse time over counts in microseconds
				pulseAverageLeft = pulseDurationLeft / countsThisLoopLeft;
				pulseDurationLeft = 0;
			}

			//Right Side
			countsThisLoopRight = pulseCountRight;
			pulseCountRight = 0;

			if (countsThisLoopRight)
			{
				//total pulse time over counts in microseconds
				pulseAverageRight = pulseDurationRight / countsThisLoopRight;
				pulseDurationRight = 0;
			}

			//increase the watchdog - reset in data recv.
			watchdogTimer++;

			//clean out serial buffer
			if (watchdogTimer > 12)
			{
				while (Serial.available() > 0) char t = Serial.read();
				watchdogTimer = 0;
			}


			//accumulated counts from this cycle
			accumulatedCountsLeft += countsThisLoopLeft;
			accumulatedCountsRight += countsThisLoopRight;

			//only if section(s) are on and there is flow
			if (countsThisLoopLeft) {    //what is current flowrate from meter
				rateKLeft = (float)pulseAverageLeft * 0.001;
				if (rateKLeft < .001) rateKLeft = 0.1;//prevent divide by zero      //
				else rateKLeft = ((1.0 / rateKLeft) * 60) / flowmeterCalFactorLeft;

				//Kalman filter
				PcLeft = PLeft + varProcessLeft;
				GLeft = PcLeft / (PcLeft + varRateLeft);
				PLeft = (1 - GLeft) * PcLeft; XpLeft = XeRateLeft; ZpLeft = XpLeft;
				XeRateLeft = GLeft * (rateKLeft - ZpLeft) + XpLeft;

				rateAppliedLPMLeft = XeRateLeft * 100; //fill in formatted rateApplied
			}
			else {
				rateKLeft = 0.1;
				rateAppliedLPMLeft = 0;
			}

			//only if section(s) are on and there is flow
			if (countsThisLoopRight) {      //what is current flowrate from meter
				rateKRight = (float)pulseAverageRight * 0.001;
				if (rateKRight < .001) rateKRight = 0.1;//prevent divide by zero    //
				else rateKRight = ((1.0 / rateKRight) * 60) / flowmeterCalFactorRight;

				//Kalman filter
				PcRight = PRight + varProcessRight;
				GRight = PcRight / (PcRight + varRateRight);
				PRight = (1 - GRight) * PcRight; XpRight = XeRateRight; ZpRight = XpRight;
				XeRateRight = GRight * (rateKRight - ZpRight) + XpRight;

				rateAppliedLPMRight = XeRateRight * 100; //fill in formatted rateApplied
			}
			else {
				rateKRight = 0.1;
				rateAppliedLPMRight = 0;
			}

			//Do the PID - this placed in code depending on valve style
			rateErrorLeft = rateSetPointLeft - rateKLeft;
			rateErrorRight = rateSetPointRight - rateKRight;

			calcRatePID();
			if (Set. RateControlLeftInst) { motorDrive(); }

			//Also needs right side TODO
			//calcRatePIDRight();
			//motorDriveRight();

			SCToAOG[2] = rateAppliedLPMLeft; //100 x actual!;
			SCToAOG[3] = rateAppliedLPMRight; //100 x actual!
			SCToAOG[4] = (int)((float)accumulatedCountsLeft / flowmeterCalFactorLeft)
				+ (int)((float)accumulatedCountsRight / flowmeterCalFactorRight);



			//print for debug
			Serial.print("Bytes to AOG: ");
			for (byte i = 0; i < 10; i++) {
				Serial.print(SCToAOG[i]);
				Serial.print(",");
			}
			Serial.println();
			Serial.flush();   // flush out buffer

		} //end of timed loop

		//****************************************************************************************
		//This runs continuously, outside of the timed loop, keeps checking UART for new data
		// header high/low, relay byte, speed byte, rateSetPoint hi/lo



	}//end of main
}
*/





//-------------------------------------------------------------------------------------------------






/*

removed: actually no rate control in AOG


//pwm variables
int pwmDrive = 0, pwmDisplay = 0;
float pValue = 0, iValue = 0, dValue = 0, drive = 0, sumSpeed = 0;
byte minPWMValue = 10;

//PID variables
float Ko = 1.0f;  //overall gain
float Kp = 1.0f;  //proportional gain
float Ki = 0.0f;//integral gain
float Kd = 0.0f;  //derivative gain

				  //integral values - **** change as required *****
int   maxIntErr = 200; //anti windup max
int maxIntegralValue = 20; //max PWM value for integral PID component

						   //error values
float lastError = 0, lastLastError = 0, integrated_error = 0, dError = 0;

void calcRatePID(void) {
	//Proportional
	pValue = 0.35 * rateErrorLeft;// *Ko;
								  /*
								  //Integral
								  integrated_error = integrated_error + rateError;
								  if (integrated_error > maxIntErr) integrated_error = maxIntErr;
								  if (integrated_error < -maxIntErr) integrated_error = -maxIntErr;

								  //once it passes near center zero out the integrator error
								  if (steerAngleError > 0) steerCurrentSign = 1;
								  else steerCurrentSign = 0;

								  //did we cross zero?
								  if (steerCurrentSign - steerPrevSign) integrated_error = 0; //zero out the integrator
								  steerPrevSign = steerCurrentSign;  //save a copy for next time

								  iValue = Ki * integrated_error;
								  if (iValue > maxIntegralValue) iValue = maxIntegralValue;
								  if (iValue < -maxIntegralValue) iValue = -maxIntegralValue;

								  //Derivative
								  dError = steerAngleError - lastLastError;
								  dValue = Kd * (dError) * Ko;

								  //save history of errors
								  lastLastError = lastError;
								  lastError = steerAngleError;
								  */
/*
	drive = pValue + dValue + iValue;

	sumSpeed += drive;
	sumSpeed = (constrain(sumSpeed, 0, 70));

	pwmDrive = int(sumSpeed);
	pwmDisplay = pwmDrive;
}

*/

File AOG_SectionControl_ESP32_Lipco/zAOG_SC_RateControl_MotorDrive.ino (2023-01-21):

void motorDrive(void)
{/*
	if (Set.RateControlLeftInst == 1) {
		//if (pwmDrive > 0) bitSet(PORTB, 4);  //set the correct direction
		//analogWrite(Set.FlowPWMLeft_PIN, pwmDrive);
	}
	else
		//manual motor drive
	{

		if (Set.Relais_MainValve_PIN < 100) { digitalWrite(Set.Relais_MainValve_PIN, Set.SectRelaysON); }
		//else { mcpForOutput.digitalWrite(Set.Relais_MainValve_PIN - 100, Set.SectRelaysON); }

		if (Set.RateControlPWM == 0)
		{	//if rate switch is toggled -> set Output high
			if (!Set.MCPInUse) {
				//WEder PCB	no MCP23017		
				if (RateManUpLeft) {
					digitalWrite(Set.FlowDirLeft_PIN, HIGH); digitalWrite(Set.FlowPWMLeft_PIN, HIGH);
					if (Set.debugmode || Set.debugmodeRelay) { Serial.println("Rate left manual up"); }
				}
				if (RateManDownLeft) {
					digitalWrite(Set.FlowDirLeft_PIN, LOW); digitalWrite(Set.FlowPWMLeft_PIN, HIGH);
					if (Set.debugmode || Set.debugmodeRelay) { Serial.println("Rate left manual down"); }
				}
				if (RateManUpRight) { digitalWrite(Set.FlowDirRight_PIN, HIGH); digitalWrite(Set.FlowPWMRight_PIN, HIGH); }
				if (RateManDownRight) { digitalWrite(Set.FlowDirRight_PIN, LOW); digitalWrite(Set.FlowPWMRight_PIN, HIGH); }
				//toggle switch not pressed = set all low
				if (!(RateManUpLeft || RateManDownLeft || RateManUpRight || RateManDownRight))
				{
					digitalWrite(Set.FlowDirRight_PIN, LOW); digitalWrite(Set.FlowPWMRight_PIN, LOW); digitalWrite(Set.FlowDirLeft_PIN, LOW); digitalWrite(Set.FlowPWMLeft_PIN, LOW);
				}
			}
			else {

			*/
				//MCP
				//Lipco mod: write into output relay bytes
				if (RateManUpLeft) {
					bitSet(RelayOUT[1], 5); bitClear(RelayOUT[1], 4);
					if (Set.debugmode || Set.debugmodeRelay) { Serial.println("Rate front manual up"); }
				}
				if (RateManDownLeft) {
					bitSet(RelayOUT[1], 4); bitClear(RelayOUT[1], 5);
					if (Set.debugmode || Set.debugmodeRelay) { Serial.println("Rate front manual down"); }
				}
				if (RateManUpRight) { bitSet(RelayOUT[1], 7); bitClear(RelayOUT[1], 6);
				if (Set.debugmode || Set.debugmodeRelay) { Serial.println("Rate rear manual up"); }
				}
				if (RateManDownRight) { bitSet(RelayOUT[1], 6); bitClear(RelayOUT[1], 7); 
				if (Set.debugmode || Set.debugmodeRelay) { Serial.println("Rate rear manual down"); }
				}
				//toggle switch not pressed = set all low
				if (!(RateManUpLeft || RateManDownLeft || RateManUpRight || RateManDownRight))
				{
					bitClear(RelayOUT[1], 4); bitClear(RelayOUT[1], 5); bitClear(RelayOUT[1], 6); bitClear(RelayOUT[1], 7);
				}
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

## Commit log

2020-01-23 PGN Data for AOG Ver 4
    [AOG Section Control PGN 8 Byte Data Description.xlsx]
2020-03-01 AOG V4 Version ESP32 & Nano 33 iot
2020-03-16 V4 ready for ESP32 and Nano33iot
2020-03-22 V4 Nano 33iot Bugfix
    [zAOG_SC_EEPROM.ino, zAOG_SC_Network.ino, zAOG_SC_WebInterface.ino]
2022-04-28 bugfix Ethernet task THX to Hans P
    [zAOG_SC_Network.ino]
2022-11-06 bugfix WiFi AP UDP
    [zAOG_SC_Network.ino]
